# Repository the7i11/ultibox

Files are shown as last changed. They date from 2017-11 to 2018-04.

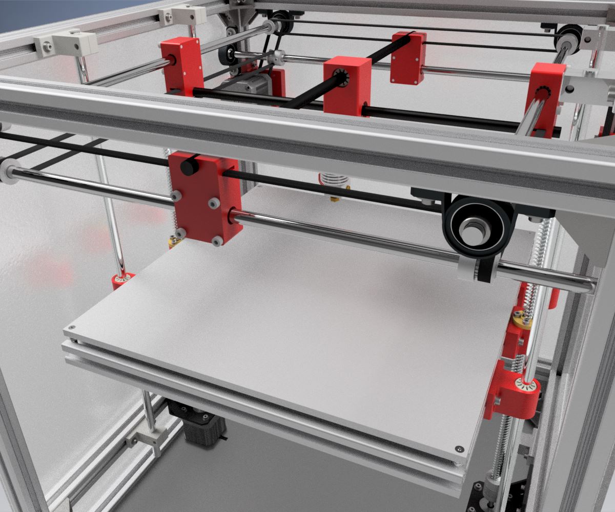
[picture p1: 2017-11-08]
media/prebuild render 05.jpg

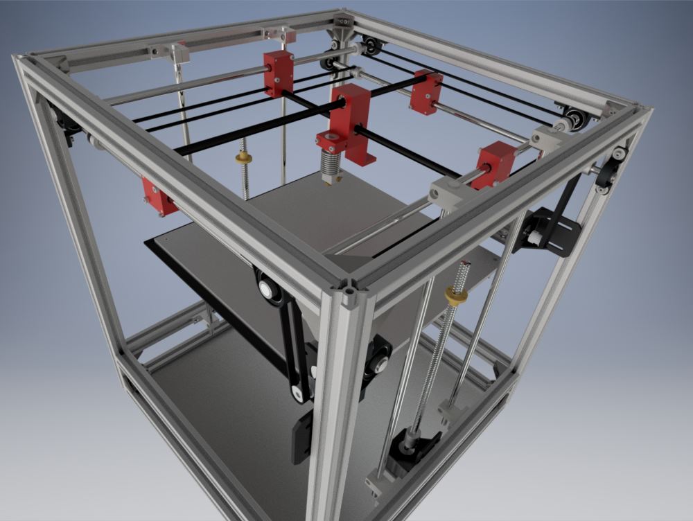
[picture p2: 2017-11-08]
media/prebuild render 03.jpg

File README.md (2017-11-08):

# Ultibox

Files for the Ultibox 3D-Printer. Please keep in mind that this project is in an early state. 
Several Ultibox 3D printers are ready-to-print at this moment, yet the project needs much work to be done.

The CAD files are created using Autodesk Inventor, but you can also use Autodesk Fusion360 to open them.

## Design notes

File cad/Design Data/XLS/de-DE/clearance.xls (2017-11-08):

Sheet: ANSI UST
I | Reihenfolge -1
Schraubentyp | Größe | Wellendurchmesser |  |  | Schraubenkopfbemaßungen
 |  | Schließen | Normal | Grob | Durchmesser | Tiefe/Winkel | Schraubenkopftyp
Flachkopfmaschinenschraube (82) | #0 | 0.0635 | 0.07 | 0.073 | 0.119 | 82 | 2
Flachkopfmaschinenschraube (82) | #1 | 0.076 | 0.081 | 0.089 | 0.146 | 82 | 2
Flachkopfmaschinenschraube (82) | #2 | 0.089 | 0.096 | 0.1065 | 0.172 | 82 | 2
Flachkopfmaschinenschraube (82) | #3 | 0.104 | 0.11 | 0.12 | 0.199 | 82 | 2
Flachkopfmaschinenschraube (82) | #4 | 0.116 | 0.1285 | 0.136 | 0.225 | 82 | 2
Flachkopfmaschinenschraube (82) | #5 | 0.1285 | 0.136 | 0.154 | 0.252 | 82 | 2
Flachkopfmaschinenschraube (82) | #6 | 0.144 | 0.1495 | 0.1695 | 0.279 | 82 | 2
Flachkopfmaschinenschraube (82) | #8 | 0.1695 | 0.177 | 0.1935 | 0.332 | 82 | 2
Flachkopfmaschinenschraube (82) | #10 | 0.196 | 0.201 | 0.221 | 0.385 | 82 | 2
Flachkopfmaschinenschraube (82) | #12 | 0.221 | 0.228 | 0.246 | 0.438 | 82 | 2
Flachkopfmaschinenschraube (82) | 1/4 | 0.257 | 0.266 | 0.2812 | 0.507 | 82 | 2
Flachkopfmaschinenschraube (82) | 5/16 | 0.323 | 0.332 | 0.3437 | 0.635 | 82 | 2
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

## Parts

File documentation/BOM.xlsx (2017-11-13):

 | Item | Count | Single | Overall
Frame
 | Aluminium extrusion 500mm | 4 | 1.34 € | 5.36 € |  | http://www.motedis.com/shop/Nutprofil/20-B-Typ-Nut-6/Aluprofil-20x20-B-Typ-Nut-6::1.html
 | Aluminium extrusion 400mm | 16 | 1.08 € | 17.28 €
 | 10 corner pieces | 4 | 2.71 € | 10.84 € |  | http://www.banggood.com/10pcs-20x20mm-Aluminium-Corner-Joint-Right-Angle-Bracket-Furniture-Fittings-p-1056722.html
 | 50 T-Nuts M3 | 2 | 3.89 € | 7.78 € |  | http://www.banggood.com/50pcs-M3-T-Sliding-Nut-Zin-Plated-Carbon-Steel-T-Sliding-Nut-for-2020-Aluminum-Profile-p-1081131.html
 | 50 M3 Washers | 2 | 1.08 € | 2.16 € |  | http://www.banggood.com/50-PCS-Stainless-Steel-Flat-Gasket-Plain-Washer-Spacer-M390_8-For-M3-Motor-Shalf-p-1064061.html
 | 100 M3x8 mm | 2 | 1.85 € | 3.70 € |  | https://www.amazon.de/St%C3%BCck-Zylinderkopfschrauben-Edelstahl-Zylinderschrauben-Innensechskant/dp/B018XL758M
 | 100 M3x20mm | 1 | 2.09 € | 2.09 € |  | https://www.amazon.de/St%C3%BCck-Zylinderkopfschrauben-Edelstahl-Zylinderschrauben-Innensechskant/dp/B018XL6B6O
 |  |  |  |  | 49.21 €
UM-Gantry
 | 2x 400 x 6mm rail | 1 | 6.89 € | 6.89 € |  | https://de.aliexpress.com/item/2-Pcs-Cnc-Linear-Shaft-Chrome-OD-6mm-L-400mm-WCS-Round-Hardened-Steel-Rod-Bar/32791713155.html
 | 4x LM8UU-formfactor bronze bushings | 1 | 7.04 € | 7.04 € |  | https://de.aliexpress.com/item/4pcs-8x15x24-mm-linear-graphite-copper-set-bearing-copper-bushing-oil-self-lubricating-bearing-JDB-Free/32823893175.html
 | 5m GT2 Belt + 4 20T Pulleys | 1 | 7.27 € | 7.27 € |  | http://www.banggood.com/GT2-Aluminium-Timing-Pulley-20-Teeth-M4-Screw-5M-Belt-For-RepRap-3D-Printer-Prusa-CNC-p-1081285.html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
 | GT2 20T double pulley 8mm bore | 2 | 1.49 € | 2.98 € |  | https://de.aliexpress.com/item/1Pcs-ultimaker-2-DIY-2GT-GT2-Timing-Driving-Pulley-20-Tooth-20teeth-Bore-5mm-8mm-Double/32640966282.html
 | 10x GT2 20T pulley 8mm bore | 1 | 8.84 € | 8.84 € |  | https://de.aliexpress.com/item/Wholesale-10pcs-20-teeth-Bore-8mm-GT2-Timing-Pulley-fit-width-6mm-of-2GT-Belt-3D/32616479146.html
 | 500 x 8mm rail | 8 | 5.95 € | 47.60 € |  | http://www.ebay.de/itm/ETGCR15-8-mm-Linearwelle-gehartet-aus-GCR15-verchromt-8-mm-Durchmesser-500-mm-/162078170839
 | 10x KP08 flanged bearing | 1 | 11.50 € | 11.50 € |  | https://de.aliexpress.com/item/NEW-10pcs-lot-8-mm-caliber-Zinc-Alloy-mounted-bearings-KP08-UCP08-P08-pillow-block-bearing/32368432549.html
 | 2x LM6LUU linear bearing | 2 | 1.00 € | 2.00 € |  | https://de.aliexpress.com/item/Free-shipping-2-pcs-lot-LM6LUU-LML6UU-6x12x35mm-6mm-Long-linear-ball-bearing-bush-bushing-Ultimaker/32727750790.html
 |  |  |  |  | 92.12 €
Z-Achse
 | Trapezoidal spindle 300mm | 2 | 2.98 € | 5.96 € |  | https://de.aliexpress.com/item/3D-Printer-THSL-300-8D-Lead-Screw-Dia-8MM-Thread-8mm-Length-300mm-trapezoidal-spindle-screw/32804077178.html
 | 4x SK8 linear rail support | 1 | 3.59 € | 3.59 € |  | https://de.aliexpress.com/item/4PCS-LOT-linear-rail-shaft-8mm-SK8-SH8A-Linear-Rail-Shaft-Support-XYZ-Table-CNC-and/32815287740.html
 | 5x8mm coupling | 2 | 1.18 € | 2.36 € |  | https://de.aliexpress.com/item/5x8-mm-Motor-Jaw-Shaft-Coupler-5mm-To-8mm-Flexible-Coupling-OD-19x25mm-Whoelsale/32615723244.html
 |  |  |  |  | 11.91 €
Extruder
 | E3D V6 all-metall clone | 1 | 8.63 € | 8.63 € |  | http://www.banggood.com/0_4mm-E3D-V6-All-metal-3D-Printer-Extrusion-Head-Nozzle-With-Fan-p-1036420.html
 | E3D Titan extruder clone | 1 | 12.87 € | 12.87 € |  | https://de.aliexpress.com/item/BIGTREETECH-Titan-Extruder-Fully-Kits-for-Titan-Extruder-for-1-75mm-Nema-17-Stepper-Motor-V6/32789942768.html
 | Induktiver proximity sensor | 1 | 1.88 € | 1.88 € |  | https://de.aliexpress.com/item/1pcs-M8-2mm-Sensing-Inductive-Proximity-Sensor-Switch-NPN-Work-Voltage-5V-DC-Special-For-MCU/32825728358.html
 | 40mm 24V fan | 1 | 0.87 € | 0.87 € |  | https://de.aliexpress.com/item/24V-2-Pin-DC-Cooling-Fan-40mm-40x40x10mm-4cm-4010s-9Blade-For-3D-Printer-CPU/32804862157.html
 |  |  |  |  | 24.25 €
Elektronik
 | Smoothieboard | 1 | 38.61 € | 38.61 € |  | https://de.aliexpress.com/item/3Dpriter-control-board-MKS-SBase-V1-0-32-s-Motherboard-compatible-Smoothieware-open-source-firmware-support/32384368763.html
 | Silikon heater matt 300x300mm | 1 | 13.94 € | 13.94 € |  | https://www.aliexpress.com/item/1pcs-silicone-heating-pad-heater-220V-600W-300-300-mm-for-3d-printer-heat-bed/32591046539.html
 | NEMA 17 stepper 0,9° 46N/cm | 2 | 12.90 € | 25.80 € |  | https://www.omc-stepperonline.com/hybrid-stepper-motor/nema-17-bipolar-09deg-46ncm-651ozin-2a-28v-42x42x48mm-4-wires-17hm19-2004s.html
 | NEMA 17 stepper 1,8° 36N/cm | 3 | 9.41 € | 28.23 € |  | https://www.omc-stepperonline.com/hybrid-stepper-motor/nema-17-bipolar-18deg-36ncm-51ozin-085a-54v-42x42x39mm-4-wires-17hs15-0854s.html
 | NEMA 17 stepper 1,8° 65N/cm | 0 | 10.26 € | 0.00 € |  | https://www.omc-stepperonline.com/hybrid-stepper-motor/nema-17-bipolar-18deg-65ncm-92ozin-21a-336v-42x42x60mm-4-wires-17hs24-2104s.html
 | 24V 5A powersupply | 1 | 12.54 € | 12.54 € |  | https://de.aliexpress.com/item/Universal-24V-5A-120W-Regulated-Switching-Power-Supply-Transformer-100-240V-AC-to-DC-For-LED/32606322171.html
 | 25A SSR 480V AC | 1 | 4.53 € | 4.53 € |  | http://www.banggood.com/SSR-25DA-SSR-Solid-state-Solid-State-Relay-25A-Output-AC24-380V-p-79300.html
 | 10 Microswitches | 1 | 1.70 € | 1.70 € |  | https://de.aliexpress.com/item/Low-Price-10pcs-Lot-3-Pin-Tact-Switch-Sensitive-Microswitch-With-Round-Handle-KW11-3Z-5A/32700243989.html
 |  |  |  |  | 125.35 €
Sonstiges
 | Fine milled aluminium plate 315x315x6mm | 1 | 34.76 € | 34.76 € |  | https://www.aluminium-online-shop.de
 | NEMA 17 mount | 2 | 2.91 € | 5.82 € |  | https://de.aliexpress.com/item/3d-printer-Accessories-NEMA17-Mounting-L-Bracket-Mount-42-series-Stepper-Motor-Alloy-Steel-Mounting-Bracket/32659632755.html
 | 50x M3 square nuts | 1 | 0.87 € | 0.87 € |  | https://de.aliexpress.com/item/100pcs-M3-color-zinc-plated-square-nuts-block-square-quadrangle-quadrilateral-galvanized-square-nuts-hw55028/32666611009.html
 |  |  |  |  | 41.45 €
 |  |  |  |  | 344.29
 |  |  |  |  |  | https://de.aliexpress.com/item/280-280-1-5mm-Silicone-Rubber-3D-Printer-Heater-220V-450w-3M-adhesive-2-face-130C/32666160575.html

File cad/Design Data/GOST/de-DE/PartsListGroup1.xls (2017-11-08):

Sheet: Лист 1
Инв. № подл |  |  |  | Подп. и дата | Взам. инв. № | Инв. № дубл. |  |  | Подп. и дата
Формат | Зона | Поз. | Обозначение |  |  |  | Наименование |  |  |  |  |  | Кол. на исполнение
 |  |  |  |  |  |  |  |  |  |  |  | Лит.
 |  |  |  |  |  |  |  |  |  |  |  | Код
 |  |  |  |  |  |  |  | Изм. | Лист | № докум | Подпись |  | Дата
 |  |  |  |  |  |  |  | Разраб.
 |  |  |  |  |  |  |  | Пров.
 |  |  |  |  |  |  |  | Н.контр
 |  |  |  |  |  |  |  | Утв.
 |  |  |  |  |  |  |  |  |  |  |  |  |  | Копировал

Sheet: Лист 2
Инв. № подл |  |  |  | Подп. и дата | Взам. инв. № | Инв. № дубл. |  |  | Подп. и дата
Формат | Зона | Поз. | Обозначение |  |  |  | Наименование |  |  |  |  | Кол. на исполнение
 |  |  |  |  |  |  |  | Изм. | Лист | № докум. | Подп. | Дата
 |  |  |  |  |  |  |  |  |  |  |  |  | Копировал
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

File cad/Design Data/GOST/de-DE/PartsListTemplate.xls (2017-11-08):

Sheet: Лист 1
 | Формат | Зона |  | Поз. |  | Обозначение |  |  |  | Наименование |  |  |  | Кол. | Приме-чание
Подп. и дата
Инв. № дубл.
Взам. инв. №
Подп. и дата
 | Изм. |  | Лист |  | № докум |  | Подпись | Дата
Инв. № подл | Разраб. |  |  |  |  |  |  |  |  |  | Литера |  | Лист |  |  | Листов
 | Пров.
 | Н.контр
 | Утв.
 |  |  |  |  |  |  |  |  | Копировал |  |  | Формат А4

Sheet: Лист 2
 | Формат | Зона |  | Поз. |  | Обозначение |  |  |  | Наименование |  | Кол. | Приме-чание
Подп. и дата
Инв. № дубл.
Взам. инв. №
Подп. и дата
Инв. № подл
 | Изм. |  | Лист |  | № докум. |  | Подп. |  | Дата
 |  |  |  |  |  |  |  | Копировал |  |  | Формат А4
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

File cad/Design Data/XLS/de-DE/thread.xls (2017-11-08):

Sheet: Inch Tapping Threads
I Q X | Zoll-Blechschraubgewinde |  | Sort Order - 5 |  | External |  |  |  |  |  |  | Internal
 |  |  |  |  |  | Major Dia |  | Pitch Dia |  | Minor Dia |  |  | Minor Dia |  | Pitch Dia |  | Major Dia |  | Tap Drill
Size | Size Suffix | Thread Designation | Custom Thread Designation | TPI | Class | Max | Min | Max | Min | Max | Min | Class | Min | Max | Min | Max | Min | Max | Basic
0.0600 |  | 0-48 | 0-48 | 48 | 2B | 0.0600 | 0.0540 | 0.0480 | 0.0435 | 0.0360 | 0.0330
0.0730 |  | 1-42 | 1-42 | 42 | 2B | 0.0750 | 0.0690 | 0.0620 | 0.0575 | 0.0490 | 0.0460
0.0860 |  | 2-32 | 2-32 | 32 | 2B | 0.0880 | 0.0820 | 0.0760 | 0.0710 | 0.0640 | 0.0600
0.0990 |  | 3-28 | 3-28 | 28 | 2B | 0.1010 | 0.0950 | 0.0880 | 0.0830 | 0.0750 | 0.0710
0.1120 |  | 4-24 | 4-24 | 24 | 2B | 0.1140 | 0.1080 | 0.1000 | 0.0950 | 0.0860 | 0.0820
0.1250 |  | 5-20 | 5-20 | 20 | 2B | 0.1300 | 0.1230 | 0.1120 | 0.1065 | 0.0940 | 0.0900
0.1380 |  | 6-20 | 6-20 | 20 | 2B | 0.1390 | 0.1320 | 0.1215 | 0.1155 | 0.1040 | 0.0990
0.1510 |  | 7-19 | 7-19 | 19 | 2B | 0.1540 | 0.1470 | 0.1345 | 0.1280 | 0.1150 | 0.1090
0.1640 |  | 8-18 | 8-18 | 18 | 2B | 0.1660 | 0.1590 | 0.1440 | 0.1375 | 0.1220 | 0.1160
0.1900 |  | 10-16 | 10-16 | 16 | 2B | 0.1890 | 0.1820 | 0.1650 | 0.1585 | 0.1410 | 0.1350
0.2160 |  | 12-14 | 12-14 | 14 | 2B | 0.2150 | 0.2080 | 0.1895 | 0.1825 | 0.1640 | 0.1570
0.2420 |  | 14-14 | 14-14 | 14 | 2B | 0.2410 | 0.2340 | 0.2130 | 0.2060 | 0.1850 | 0.1780
0.2500 |  | 1/4-14 | 1/4-14 | 14 | 2B | 0.2460 | 0.2370 | 0.2190 | 0.2110 | 0.1920 | 0.1850
0.3125 |  | 5/16-12 | 5/16-12 | 12 | 2B | 0.3150 | 0.3060 | 0.2795 | 0.2710 | 0.2440 | 0.2360
0.3750 |  | 3/8-12 | 3/8-12 | 12 | 2B | 0.3800 | 0.3710 | 0.3445 | 0.3350 | 0.3090 | 0.2990
0.4375 |  | 7/16-10 | 7/16-10 | 10 | 2B | 0.4400 | 0.4290 | 0.3995 | 0.3890 | 0.3590 | 0.3490
0.5000 |  | 1/2-10 | 1/2-10 | 10 | 2B | 0.5040 | 0.4930 | 0.4635 | 0.4530 | 0.4230 | 0.4130

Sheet: Metric Forming Screw Threads
M P X | Metrisch geform. Schraubgewinde |  | Sort Order - 6 |  | External |  |  |  |  |  |  | Internal
 |  |  |  |  |  | Major Dia |  | Pitch Dia |  | Minor Dia |  |  | Minor Dia |  | Pitch Dia |  | Major Dia |  | Tap Drill
Size | Size Suffix | Thread Designation | Custom Thread Designation | Pitch | Class | Max | Min | Max | Min | Max | Min | Class | Min | Max | Min | Max | Min | Max | Basic
1.5 |  | 1.5x0.5 | 1.5x0.5 | 0.5 | 6g | 1.520 | 1.380 | 1.215 | 1.110 | 0.910 | 0.840
1.5 |  | ST1.5x0.5 | ST1.5x0.5 | 0.5 | 6g | 1.520 | 1.380 | 1.215 | 1.110 | 0.910 | 0.840
1.9 |  | 1.9x0.6 | 1.9x0.6 | 0.6 | 6g | 1.900 | 1.760 | 1.570 | 1.465 | 1.240 | 1.170
1.9 |  | ST1.9x0.6 | ST1.9x0.6 | 0.6 | 6g | 1.900 | 1.760 | 1.570 | 1.465 | 1.240 | 1.170
2.2 |  | 2.2x0.8 | 2.2x0.8 | 0.8 | 6g | 2.240 | 2.100 | 1.935 | 1.810 | 1.630 | 1.520
2.2 |  | ST2.2x0.8 | ST2.2x0.8 | 0.8 | 6g | 2.240 | 2.100 | 1.935 | 1.810 | 1.630 | 1.520
2.6 |  | 2.6x0.9 | 2.6x0.9 | 0.9 | 6g | 2.570 | 2.430 | 2.235 | 2.115 | 1.900 | 1.800
2.6 |  | ST2.6x0.9 | ST2.6x0.9 | 0.9 | 6g | 2.570 | 2.430 | 2.235 | 2.115 | 1.900 | 1.800
2.9 |  | 2.9x1 | 2.9x1 | 1 | 6g | 2.900 | 2.760 | 2.540 | 2.420 | 2.180 | 2.080
2.9 |  | 2.9x1.1 | 2.9x1.1 | 1.1 | 6g | 2.900 | 2.760 | 2.540 | 2.420 | 2.180 | 2.080
2.9 |  | ST2.9x1.1 | ST2.9x1.1 | 1.1 | 6g | 2.900 | 2.760 | 2.540 | 2.420 | 2.180 | 2.080
2.9 |  | 2.9x1.3 | 2.9x1.3 | 1.3 | 6g | 2.900 | 2.720 | 2.540 | 2.355 | 1.890 | 1.700
2.9 |  | 2.9x1.4 | 2.9x1.4 | 1.4 | 6g | 2.900 | 2.720 | 2.340 | 2.175 | 1.780 | 1.630
3.3 |  | 3.3x1.3 | 3.3x1.3 | 1.3 | 6g | 3.300 | 3.120 | 2.795 | 2.665 | 2.290 | 2.210
3.3 |  | ST3.3x1.3 | ST3.3x1.3 | 1.3 | 6g | 3.300 | 3.120 | 2.795 | 2.665 | 2.290 | 2.210
3.5 |  | 3.5x1.3 | 3.5x1.3 | 1.3 | 6g | 3.530 | 3.350 | 3.085 | 2.930 | 2.640 | 2.510
3.5 |  | ST3.5x1.3 | ST3.5x1.3 | 1.3 | 6g | 3.530 | 3.350 | 3.085 | 2.930 | 2.640 | 2.510
3.5 |  | 3.5x1.6 | 3.5x1.6 | 1.6 | 6g | 3.530 | 3.350 | 2.920 | 2.755 | 2.310 | 2.160
3.5 |  | 3.5x3.2 | 3.5x3.2 | 3.2 | 6g | 3.530 | 3.310 | 2.800 | 2.600 | 2.070 | 1.890
3.9 |  | 3.9x1.3 | 3.9x1.3 | 1.3 | 6g | 3.910 | 3.730 | 3.415 | 3.250 | 2.920 | 2.770
3.9 |  | ST3.9x1.3 | ST3.9x1.3 | 1.3 | 6g | 3.910 | 3.730 | 3.415 | 3.250 | 2.920 | 2.770
3.9 |  | 3.9x1.6 | 3.9x1.6 | 1.6 | 6g | 3.910 | 3.730 | 3.300 | 3.135 | 2.690 | 2.540
3.9 |  | 3.9x3.2 | 3.9x3.2 | 3.2 | 6g | 3.910 | 3.690 | 3.180 | 2.980 | 2.450 | 2.270
4.2 |  | 4.2x1.4 | 4.2x1.4 | 1.4 | 6g | 4.220 | 4.040 | 3.660 | 3.495 | 3.100 | 2.950
4.2 |  | ST4.2x1.4 | ST4.2x1.4 | 1.4 | 6g | 4.220 | 4.040 | 3.660 | 3.495 | 3.100 | 2.950
4.2 |  | 4.2x1.6 | 4.2x1.6 | 1.6 | 6g | 4.220 | 4.040 | 3.610 | 3.445 | 3.000 | 2.850
4.2 |  | 4.2x3.2 | 4.2x3.2 | 3.2 | 6g | 4.220 | 4.000 | 3.380 | 3.180 | 2.540 | 2.360
4.8 |  | 4.8x1.6 | 4.8x1.6 | 1.6 | 6g | 4.800 | 4.620 | 4.190 | 4.025 | 3.580 | 3.430
4.8 |  | ST4.8x1.6 | ST4.8x1.6 | 1.6 | 6g | 4.800 | 4.620 | 4.190 | 4.025 | 3.580 | 3.430
4.8 |  | 4.8x1.8 | 4.8x1.8 | 1.8 | 6g | 4.800 | 4.620 | 4.065 | 3.885 | 3.330 | 3.150
4.8 |  | 4.8x3.2 | 4.8x3.2 | 3.2 | 6g | 4.800 | 4.580 | 3.960 | 3.760 | 3.120 | 2.940
5.5 |  | 5.5x1.8 | 5.5x1.8 | 1.8 | 6g | 5.460 | 5.280 | 4.815 | 4.635 | 4.170 | 3.990
5.5 |  | ST5.5x1.8 | ST5.5x1.8 | 1.8 | 6g | 5.460 | 5.280 | 4.815 | 4.635 | 4.170 | 3.990
6.3 |  | 6.3x1.8 | 6.3x1.8 | 1.8 | 6g | 6.250 | 6.030 | 5.565 | 5.365 | 4.880 | 4.700
6.3 |  | ST6.3x1.8 | ST6.3x1.8 | 1.8 | 6g | 6.250 | 6.030 | 5.565 | 5.365 | 4.880 | 4.700
8.0 |  | 8x2.1 | 8x2.1 | 2.1 | 6g | 8.000 | 7.780 | 7.100 | 6.885 | 6.200 | 5.990
8.0 |  | ST8x2.1 | ST8x2.1 | 2.1 | 6g | 8.000 | 7.780 | 7.100 | 6.885 | 6.200 | 5.990
9.5 |  | 9.5x2.1 | 9.5x2.1 | 2.1 | 6g | 9.650 | 9.430 | 8.750 | 8.510 | 7.850 | 7.590
9.5 |  | ST9.5x2.1 | ST9.5x2.1 | 2.1 | 6g | 9.650 | 9.430 | 8.750 | 8.510 | 7.850 | 7.590

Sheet: ISO Pipe Threads
M Q | ISO-Rohrgewinde |  | Sort Order - 9 |  | External |  |  |  |  |  |  | Internal
 |  |  |  |  |  | Major Dia |  | Pitch Dia |  | Minor Dia |  |  | Minor Dia |  | Pitch Dia |  | Major Dia |  | Tap Drill | Thread Depth | Thread Runouts
Size | Size Suffix | Thread Designation | Custom Thread Designation | TPI | Class | Max | Min | Max | Min | Max | Min | Class | Min | Max | Min | Max | Min | Max | Basic
7.723 |  | G7.723x0.907 | G 1/16 | 28 | A | 7.723 | 7.509 | 7.142 | 7.035 | 6.561 |  |  | 6.561 | 6.834 | 7.142 | 7.249 | 7.723 |  | 1.5875 | 15.446 | 4.5000
7.723 |  | G7.723x0.907 | G 1/16 | 28 | B | 7.723 | 7.509 | 7.142 | 6.928 | 6.561
9.728 |  | G9.728x0.907 | G 1/8 | 28 | A | 9.728 | 9.514 | 9.147 | 9.040 | 8.566 |  |  | 8.566 | 8.848 | 9.147 | 9.254 | 9.728 |  | 3.1750 | 19.456 | 4.5000
9.728 |  | G9.728x0.907 | G 1/8 | 28 | B | 9.728 | 9.514 | 9.147 | 8.933 | 8.566
13.157 |  | G13.157x1.337 | G 1/4 | 19 | A | 13.157 | 12.907 | 12.301 | 12.176 | 11.445 |  |  | 11.445 | 11.89 | 12.301 | 12.426 | 13.157 |  | 6.3500 | 26.314 | 6.5000
13.157 |  | G13.157x1.337 | G 1/4 | 19 | B | 13.157 | 12.907 | 12.301 | 12.051 | 11.445
16.662 |  | G16.662x1.337 | G 3/8 | 19 | A | 16.662 | 16.412 | 15.806 | 15.681 | 14.950 |  |  | 14.95 | 15.395 | 15.806 | 15.931 | 16.662 |  | 9.5250 | 33.324 | 6.5000
16.662 |  | G16.662x1.337 | G 3/8 | 19 | B | 16.662 | 16.412 | 15.806 | 15.556 | 14.950
20.955 |  | G20.955x1.814 | G 1/2 | 14 | A | 20.955 | 20.671 | 19.793 | 19.651 | 18.631 |  |  | 18.631 | 19.172 | 19.793 | 19.935 | 20.955 |  | 12.7000 | 41.910 | 8.5000
20.955 |  | G20.955x1.814 | G 1/2 | 14 | B | 20.955 | 20.671 | 19.793 | 19.509 | 18.631
22.911 |  | G22.911x1.814 | G 5/8 | 14 | A | 22.911 | 22.627 | 21.749 | 21.607 | 20.587 |  |  | 20.587 | 21.128 | 21.749 | 21.891 | 22.911 |  |  | 45.822 | 8.5000
22.911 |  | G22.911x1.814 | G 5/8 | 14 | B | 22.911 | 22.627 | 21.749 | 21.465 | 20.587
26.441 |  | G26.441x1.814 | G 3/4 | 14 | A | 26.441 | 26.157 | 25.279 | 25.137 | 24.117 |  |  | 24.117 | 24.658 | 25.279 | 25.421 | 26.441 |  | 15.8750 | 52.882 | 8.5000
26.441 |  | G26.441x1.814 | G 3/4 | 14 | B | 26.441 | 26.157 | 25.279 | 24.995 | 24.117
30.201 |  | G30.201x1.814 | G 7/8 | 14 | A | 30.201 | 29.917 | 29.039 | 28.897 | 27.877 |  |  | 27.877 | 28.418 | 29.039 | 29.181 | 30.201 |  | 22.2250 | 60.402 | 8.5000
30.201 |  | G30.201x1.814 | G 7/8 | 14 | B | 30.201 | 29.917 | 29.039 | 28.755 | 27.877
33.249 |  | G33.249x2.309 | G 1 | 11 | A | 33.249 | 32.889 | 31.770 | 31.590 | 30.291 |  |  | 30.291 | 30.931 | 31.77 | 31.95 | 33.249 |  | 25.4000 | 66.498 | 10.0000
33.249 |  | G33.249x2.309 | G 1 | 11 | B | 33.249 | 32.889 | 31.770 | 31.410 | 30.291
37.897 |  | G37.897x2.309 | G 1 1/8 | 11 | A | 37.897 | 37.537 | 36.418 | 36.238 | 34.939 |  |  | 34.939 | 35.579 | 36.418 | 36.598 | 37.897 |  | 28.5750 | 75.794 | 10.0000
37.897 |  | G37.897x2.309 | G 1 1/8 | 11 | B | 37.897 | 37.537 | 36.418 | 36.058 | 34.939
41.910 |  | G41.91x2.309 | G 1 1/4 | 11 | A | 41.910 | 41.550 | 40.431 | 40.251 | 38.952 |  |  | 38.952 | 39.592 | 40.431 | 40.611 | 41.910 |  | 31.7500 | 83.820 | 10.0000
41.910 |  | G41.91x2.309 | G 1 1/4 | 11 | B | 41.910 | 41.550 | 40.431 | 40.071 | 38.952
47.803 |  | G47.803x2.309 | G 1 1/2 | 11 | A | 47.803 | 47.443 | 46.324 | 46.144 | 44.845 |  |  | 44.845 | 45.485 | 46.324 | 46.504 | 47.803 |  | 38.1000 | 95.606 | 10.0000
47.803 |  | G47.803x2.309 | G 1 1/2 | 11 | B | 47.803 | 47.443 | 46.324 | 45.964 | 44.845
53.746 |  | G53.746x2.309 | G 1 3/4 | 11 | A | 53.746 | 53.386 | 52.267 | 52.087 | 50.788 |  |  | 50.788 | 51.428 | 52.267 | 52.447 | 53.746 |  | 44.4500 | 107.492 | 10.0000
53.746 |  | G53.746x2.309 | G 1 3/4 | 11 | B | 53.746 | 53.386 | 52.267 | 51.907 | 50.788
59.614 |  | G59.614x2.309 | G 2 | 11 | A | 59.614 | 59.254 | 58.135 | 57.955 | 56.656 |  |  | 56.656 | 57.296 | 58.135 | 58.315 | 59.614 |  | 50.8000 | 119.228 | 10.0000
59.614 |  | G59.614x2.309 | G 2 | 11 | B | 59.614 | 59.254 | 58.135 | 57.775 | 56.656
65.710 |  | G65.71x2.309 | G 2 1/4 | 11 | A | 65.710 | 65.276 | 64.231 | 64.014 | 62.752 |  |  | 62.752 | 63.392 | 64.231 | 64.448 | 65.710 |  | 57.1500 | 131.420 | 10.0000
65.710 |  | G65.71x2.309 | G 2 1/4 | 11 | B | 65.710 | 65.276 | 64.231 | 63.797 | 62.752
75.184 |  | G75.184x2.309 | G 2 1/2 | 11 | A | 75.184 | 74.750 | 73.705 | 73.488 | 72.226 |  |  | 72.226 | 72.866 | 73.705 | 73.922 | 75.184 |  |  | 150.368 | 10.0000
75.184 |  | G75.184x2.309 | G 2 1/2 | 11 | B | 75.184 | 74.750 | 73.705 | 73.271 | 72.226
81.534 |  | G81.534x2.309 | G 2 3/4 | 11 | A | 81.534 | 81.100 | 80.055 | 79.838 | 78.576 |  |  | 78.576 | 79.216 | 80.055 | 80.272 | 81.534 |  | 69.8500 | 163.068 | 10.0000
81.534 |  | G81.534x2.309 | G 2 3/4 | 11 | B | 81.534 | 81.100 | 80.055 | 79.621 | 78.576
87.884 |  | G87.884x2.309 | G 3 | 11 | A | 87.884 | 87.450 | 86.405 | 86.188 | 84.926 |  |  | 84.926 | 85.566 | 86.405 | 86.622 | 87.884 |  | 76.2000 | 175.768 | 10.0000
87.884 |  | G87.884x2.309 | G 3 | 11 | B | 87.884 | 87.450 | 86.405 | 85.971 | 84.926
100.330 |  | G100.33x2.309 | G 3 1/2 | 11 | A | 100.330 | 99.896 | 98.851 | 98.634 | 97.372 |  |  | 97.372 | 98.012 | 98.851 | 99.068 | 100.330 |  | 88.9000 | 200.660 | 10.0000
100.330 |  | G100.33x2.309 | G 3 1/2 | 11 | B | 100.330 | 99.896 | 98.851 | 98.417 | 97.372
113.030 |  | G113.03x2.309 | G 4 | 11 | A | 113.030 | 112.596 | 111.551 | 111.334 | 110.072 |  |  | 110.072 | 110.712 | 111.551 | 111.768 | 113.030 |  | 101.6000 | 226.060 | 10.0000
113.030 |  | G113.03x2.309 | G 4 | 11 | B | 113.030 | 112.596 | 111.551 | 111.117 | 110.072
125.730 |  | G125.73x2.309 | G 4 1/2 | 11 | A | 125.730 | 125.296 | 124.251 | 124.034 | 122.772 |  |  | 122.772 | 123.412 | 124.251 | 124.468 | 125.730 |  | 114.3000 | 251.460 | 10.0000
125.730 |  | G125.73x2.309 | G 4 1/2 | 11 | B | 125.730 | 125.296 | 124.251 | 123.817 | 122.772
138.430 |  | G138.43x2.309 | G 5 | 11 | A | 138.430 | 137.996 | 136.951 | 136.734 | 135.472 |  |  | 135.472 | 136.112 | 136.951 | 137.168 | 138.430 |  | 127.0000 | 276.860 | 10.0000
138.430 |  | G138.43x2.309 | G 5 | 11 | B | 138.430 | 137.996 | 136.951 | 136.517 | 135.472
151.130 |  | G151.13x2.309 | G 5 1/2 | 11 | A | 151.130 | 150.696 | 149.651 | 149.434 | 148.172 |  |  | 148.172 | 148.812 | 149.651 | 149.868 | 151.130 |  | 139.7000 | 302.260 | 10.0000
151.130 |  | G151.13x2.309 | G 5 1/2 | 11 | B | 151.130 | 150.696 | 149.651 | 149.217 | 148.172
163.830 |  | G163.83x2.309 | G 6 | 11 | A | 163.830 | 163.396 | 162.351 | 162.134 | 160.872 |  |  | 160.872 | 161.512 | 162.351 | 162.568 | 163.830 |  | 152.4000 | 327.660 | 10.0000
163.830 |  | G163.83x2.309 | G 6 | 11 | B | 163.830 | 163.396 | 162.351 | 161.917 | 160.872

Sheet: JIS Pipe Threads
M Q | JIS-Rohrgewinde |  | Sort Order -12 |  | External |  |  |  |  |  |  | Internal
 |  |  |  |  |  | Major Dia |  | Pitch Dia |  | Minor Dia |  |  | Minor Dia |  | Pitch Dia |  | Major Dia |  | Tap Drill | Thread Depth | Thread Runouts
Size | Size Suffix | Thread Designation | Custom Thread Designation | TPI | Class | Max | Min | Max | Min | Max | Min | Class | Min | Max | Min | Max | Min | Max | Basic |  | Basic
7.723 |  | G7.723x0.907 | G 1/16 | 28 | A | 7.723 | 7.509 | 7.142 | 7.035 | 6.561 |  |  | 6.561 | 6.834 | 7.142 | 7.249 | 7.723 |  | 1.5875 | 15.446 | 4.5000
7.723 |  | G7.723x0.907 | G 1/16 | 28 | B | 7.723 | 7.509 | 7.142 | 6.928 | 6.561
9.728 |  | G9.728x0.907 | G 1/8 | 28 | A | 9.728 | 9.514 | 9.147 | 9.040 | 8.566 |  |  | 8.566 | 8.848 | 9.147 | 9.254 | 9.728 |  | 3.1750 | 19.456 | 4.5000
9.728 |  | G9.728x0.907 | G 1/8 | 28 | B | 9.728 | 9.514 | 9.147 | 8.933 | 8.566
13.157 |  | G13.157x1.337 | G 1/4 | 19 | A | 13.157 | 12.907 | 12.301 | 12.176 | 11.445 |  |  | 11.445 | 11.89 | 12.301 | 12.426 | 13.157 |  | 6.3500 | 26.314 | 6.5000
13.157 |  | G13.157x1.337 | G 1/4 | 19 | B | 13.157 | 12.907 | 12.301 | 12.051 | 11.445
16.662 |  | G16.662x1.337 | G 3/8 | 19 | A | 16.662 | 16.412 | 15.806 | 15.681 | 14.950 |  |  | 14.95 | 15.395 | 15.806 | 15.931 | 16.662 |  | 9.5250 | 33.324 | 6.5000
16.662 |  | G16.662x1.337 | G 3/8 | 19 | B | 16.662 | 16.412 | 15.806 | 15.556 | 14.950
20.955 |  | G20.955x1.814 | G 1/2 | 14 | A | 20.955 | 20.671 | 19.793 | 19.651 | 18.631 |  |  | 18.631 | 19.172 | 19.793 | 19.935 | 20.955 |  | 12.7000 | 41.910 | 8.5000
20.955 |  | G20.955x1.814 | G 1/2 | 14 | B | 20.955 | 20.671 | 19.793 | 19.509 | 18.631
22.911 |  | G22.911x1.814 | G 5/8 | 14 | A | 22.911 | 22.627 | 21.749 | 21.607 | 20.587 |  |  | 20.587 | 21.128 | 21.749 | 21.891 | 22.911 |  |  | 45.822 | 8.5000
22.911 |  | G22.911x1.814 | G 5/8 | 14 | B | 22.911 | 22.627 | 21.749 | 21.465 | 20.587
26.441 |  | G26.441x1.814 | G 3/4 | 14 | A | 26.441 | 26.157 | 25.279 | 25.137 | 24.117 |  |  | 24.117 | 24.658 | 25.279 | 25.421 | 26.441 |  | 15.8750 | 52.882 | 8.5000
26.441 |  | G26.441x1.814 | G 3/4 | 14 | B | 26.441 | 26.157 | 25.279 | 24.995 | 24.117
30.201 |  | G30.201x1.814 | G 7/8 | 14 | A | 30.201 | 29.917 | 29.039 | 28.897 | 27.877 |  |  | 27.877 | 28.418 | 29.039 | 29.181 | 30.201 |  | 22.2250 | 60.402 | 8.8000
30.201 |  | G30.201x1.814 | G 7/8 | 14 | B | 30.201 | 29.917 | 29.039 | 28.755 | 27.877
33.249 |  | G33.249x2.309 | G 1 | 11 | A | 33.249 | 32.889 | 31.770 | 31.590 | 30.291 |  |  | 30.291 | 30.931 | 31.77 | 31.95 | 33.249 |  | 25.4000 | 66.498 | 10.0000
33.249 |  | G33.249x2.309 | G 1 | 11 | B | 33.249 | 32.889 | 31.770 | 31.410 | 30.291
37.897 |  | G37.897x2.309 | G 1 1/8 | 11 | A | 37.897 | 37.537 | 36.418 | 36.238 | 34.939 |  |  | 34.939 | 35.579 | 36.418 | 36.598 | 37.897 |  | 28.5750 | 75.794 | 10.0000
37.897 |  | G37.897x2.309 | G 1 1/8 | 11 | B | 37.897 | 37.537 | 36.418 | 36.058 | 34.939
41.910 |  | G41.91x2.309 | G 1 1/4 | 11 | A | 41.910 | 41.550 | 40.431 | 40.251 | 38.952 |  |  | 38.952 | 39.592 | 40.431 | 40.611 | 41.910 |  | 31.7500 | 83.820 | 10.0000
41.910 |  | G41.91x2.309 | G 1 1/4 | 11 | B | 41.910 | 41.550 | 40.431 | 40.071 | 38.952
47.803 |  | G47.803x2.309 | G 1 1/2 | 11 | A | 47.803 | 47.443 | 46.324 | 46.144 | 44.845 |  |  | 44.845 | 45.485 | 46.324 | 46.504 | 47.803 |  | 38.1000 | 95.606 | 10.0000
47.803 |  | G47.803x2.309 | G 1 1/2 | 11 | B | 47.803 | 47.443 | 46.324 | 45.964 | 44.845
53.746 |  | G53.746x2.309 | G 1 3/4 | 11 | A | 53.746 | 53.386 | 52.267 | 52.087 | 50.788 |  |  | 50.788 | 51.428 | 52.267 | 52.447 | 53.746 |  | 44.4500 | 107.492 | 10.0000
53.746 |  | G53.746x2.309 | G 1 3/4 | 11 | B | 53.746 | 53.386 | 52.267 | 51.907 | 50.788
59.614 |  | G59.614x2.309 | G 2 | 11 | A | 59.614 | 59.254 | 58.135 | 57.955 | 56.656 |  |  | 56.656 | 57.296 | 58.135 | 58.315 | 59.614 |  | 50.8000 | 119.228 | 10.0000
59.614 |  | G59.614x2.309 | G 2 | 11 | B | 59.614 | 59.254 | 58.135 | 57.775 | 56.656
65.710 |  | G65.71x2.309 | G 2 1/4 | 11 | A | 65.710 | 65.276 | 64.231 | 64.014 | 62.752 |  |  | 62.752 | 63.392 | 64.231 | 64.448 | 65.710 |  | 57.1500 | 131.420 | 10.0000
65.710 |  | G65.71x2.309 | G 2 1/4 | 11 | B | 65.710 | 65.276 | 64.231 | 63.797 | 62.752
75.184 |  | G75.184x2.309 | G 2 1/2 | 11 | A | 75.184 | 74.750 | 73.705 | 73.488 | 72.226 |  |  | 72.226 | 72.866 | 73.705 | 73.922 | 75.184 |  |  | 150.368 | 10.0000
75.184 |  | G75.184x2.309 | G 2 1/2 | 11 | B | 75.184 | 74.750 | 73.705 | 73.271 | 72.226
81.534 |  | G81.534x2.309 | G 2 3/4 | 11 | A | 81.534 | 81.100 | 80.055 | 79.838 | 78.576 |  |  | 78.576 | 79.216 | 80.055 | 80.272 | 81.534 |  | 69.8500 | 163.068 | 10.0000
81.534 |  | G81.534x2.309 | G 2 3/4 | 11 | B | 81.534 | 81.100 | 80.055 | 79.621 | 78.576
87.884 |  | G87.884x2.309 | G 3 | 11 | A | 87.884 | 87.450 | 86.405 | 86.188 | 84.926 |  |  | 84.926 | 85.566 | 86.405 | 86.622 | 87.884 |  | 76.2000 | 175.768 | 10.0000
87.884 |  | G87.884x2.309 | G 3 | 11 | B | 87.884 | 87.450 | 86.405 | 85.971 | 84.926
100.330 |  | G100.33x2.309 | G 3 1/2 | 11 | A | 100.330 | 99.896 | 98.851 | 98.634 | 97.372 |  |  | 97.372 | 98.012 | 98.851 | 99.068 | 100.330 |  | 88.9000 | 200.660 | 10.0000
100.330 |  | G100.33x2.309 | G 3 1/2 | 11 | B | 100.330 | 99.896 | 98.851 | 98.417 | 97.372
113.030 |  | G113.03x2.309 | G 4 | 11 | A | 113.030 | 112.596 | 111.551 | 111.334 | 110.072 |  |  | 110.072 | 110.712 | 111.551 | 111.768 | 113.030 |  | 101.6000 | 226.060 | 10.0000
113.030 |  | G113.03x2.309 | G 4 | 11 | B | 113.030 | 112.596 | 111.551 | 111.117 | 110.072
125.730 |  | G125.73x2.309 | G 4 1/2 | 11 | A | 125.730 | 125.296 | 124.251 | 124.034 | 122.772 |  |  | 122.772 | 123.412 | 124.251 | 124.468 | 125.730 |  | 114.3000 | 251.460 | 10.0000
125.730 |  | G125.73x2.309 | G 4 1/2 | 11 | B | 125.730 | 125.296 | 124.251 | 123.817 | 122.772
138.430 |  | G138.43x2.309 | G 5 | 11 | A | 138.430 | 137.996 | 136.951 | 136.734 | 135.472 |  |  | 135.472 | 136.112 | 136.951 | 137.168 | 138.430 |  | 127.0000 | 276.860 | 10.0000
138.430 |  | G138.43x2.309 | G 5 | 11 | B | 138.430 | 137.996 | 136.951 | 136.517 | 135.472
151.130 |  | G151.13x2.309 | G 5 1/2 | 11 | A | 151.130 | 150.696 | 149.651 | 149.434 | 148.172 |  |  | 148.172 | 148.812 | 149.651 | 149.868 | 151.130 |  | 139.7000 | 302.260 | 10.0000
151.130 |  | G151.13x2.309 | G 5 1/2 | 11 | B | 151.130 | 150.696 | 149.651 | 149.217 | 148.172
163.830 |  | G163.83x2.309 | G 6 | 11 | A | 163.830 | 163.396 | 162.351 | 162.134 | 160.872 |  |  | 160.872 | 161.512 | 162.351 | 162.568 | 163.830 |  | 152.4000 | 327.660 | 10.0000
163.830 |  | G163.83x2.309 | G 6 | 11 | B | 163.830 | 163.396 | 162.351 | 161.917 | 160.872

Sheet: DIN Pipe Threads
M Q | DIN-Rohrgewinde |  | Sort Order - 18 |  | External |  |  |  |  |  |  | Internal
 |  |  |  |  |  | Major Dia |  | Pitch Dia |  | Minor Dia |  |  | Minor Dia |  | Pitch Dia |  | Major Dia |  | Tap Drill | Thread Depth | Thread Runouts
Size | Size Suffix | Thread Designation | Custom Thread Designation | TPI | Class | Max | Min | Max | Min | Max | Min | Class | Min | Max | Min | Max | Min | Max | Basic
7.723 |  | G7.723x0.907 | G 1/16 | 28 | A | 7.723 | 7.509 | 7.142 | 7.035 | 6.561 |  |  | 6.561 | 6.834 | 7.142 | 7.249 | 7.723 |  | 1.5875 | 15.446 | 4.5000
7.723 |  | G7.723x0.907 | G 1/16 | 28 | B | 7.723 | 7.509 | 7.142 | 6.928 | 6.561
9.728 |  | G9.728x0.907 | G 1/8 | 28 | A | 9.728 | 9.514 | 9.147 | 9.040 | 8.566 |  |  | 8.566 | 8.848 | 9.147 | 9.254 | 9.728 |  | 3.1750 | 19.456 | 4.5000
9.728 |  | G9.728x0.907 | G 1/8 | 28 | B | 9.728 | 9.514 | 9.147 | 8.933 | 8.566
13.157 |  | G13.157x1.337 | G 1/4 | 19 | A | 13.157 | 12.907 | 12.301 | 12.176 | 11.445 |  |  | 11.445 | 11.89 | 12.301 | 12.426 | 13.157 |  | 6.3500 | 26.314 | 6.5000
13.157 |  | G13.157x1.337 | G 1/4 | 19 | B | 13.157 | 12.907 | 12.301 | 12.051 | 11.445
16.662 |  | G16.662x1.337 | G 3/8 | 19 | A | 16.662 | 16.412 | 15.806 | 15.681 | 14.950 |  |  | 14.95 | 15.395 | 15.806 | 15.931 | 16.662 |  | 9.5250 | 33.324 | 6.5000
16.662 |  | G16.662x1.337 | G 3/8 | 19 | B | 16.662 | 16.412 | 15.806 | 15.556 | 14.950
20.955 |  | G20.955x1.814 | G 1/2 | 14 | A | 20.955 | 20.671 | 19.793 | 19.651 | 18.631 |  |  | 18.631 | 19.172 | 19.793 | 19.935 | 20.955 |  | 12.7000 | 41.910 | 8.5000
20.955 |  | G20.955x1.814 | G 1/2 | 14 | B | 20.955 | 20.671 | 19.793 | 19.509 | 18.631
22.911 |  | G22.911x1.814 | G 5/8 | 14 | A | 22.911 | 22.627 | 21.749 | 21.607 | 20.587 |  |  | 20.587 | 21.128 | 21.749 | 21.891 | 22.911 |  |  | 45.822 | 8.5000
22.911 |  | G22.911x1.814 | G 5/8 | 14 | B | 22.911 | 22.627 | 21.749 | 21.465 | 20.587
26.441 |  | G26.441x1.814 | G 3/4 | 14 | A | 26.441 | 26.157 | 25.279 | 25.137 | 24.117 |  |  | 24.117 | 24.658 | 25.279 | 25.421 | 26.441 |  | 15.8750 | 52.882 | 8.5000
26.441 |  | G26.441x1.814 | G 3/4 | 14 | B | 26.441 | 26.157 | 25.279 | 24.995 | 24.117
30.201 |  | G30.201x1.814 | G 7/8 | 14 | A | 30.201 | 29.917 | 29.039 | 28.897 | 27.877 |  |  | 27.877 | 28.418 | 29.039 | 29.181 | 30.201 |  | 22.2250 | 60.402 | 8.5000
30.201 |  | G30.201x1.814 | G 7/8 | 14 | B | 30.201 | 29.917 | 29.039 | 28.755 | 27.877
33.249 |  | G33.249x2.309 | G 1 | 11 | A | 33.249 | 32.889 | 31.770 | 31.590 | 30.291 |  |  | 30.291 | 30.931 | 31.77 | 31.95 | 33.249 |  | 25.4000 | 66.498 | 10.5000
33.249 |  | G33.249x2.309 | G 1 | 11 | B | 33.249 | 32.889 | 31.770 | 31.410 | 30.291
37.897 |  | G37.897x2.309 | G 1 1/8 | 11 | A | 37.897 | 37.537 | 36.418 | 36.238 | 34.939 |  |  | 34.939 | 35.579 | 36.418 | 36.598 | 37.897 |  | 28.5750 | 75.794 | 10.5000
37.897 |  | G37.897x2.309 | G 1 1/8 | 11 | B | 37.897 | 37.537 | 36.418 | 36.058 | 34.939
41.910 |  | G41.91x2.309 | G 1 1/4 | 11 | A | 41.910 | 41.550 | 40.431 | 40.251 | 38.952 |  |  | 38.952 | 39.592 | 40.431 | 40.611 | 41.910 |  | 31.7500 | 83.820 | 10.5000
41.910 |  | G41.91x2.309 | G 1 1/4 | 11 | B | 41.910 | 41.550 | 40.431 | 40.071 | 38.952
47.803 |  | G47.803x2.309 | G 1 1/2 | 11 | A | 47.803 | 47.443 | 46.324 | 46.144 | 44.845 |  |  | 44.845 | 45.485 | 46.324 | 46.504 | 47.803 |  | 38.1000 | 95.606 | 10.5000
47.803 |  | G47.803x2.309 | G 1 1/2 | 11 | B | 47.803 | 47.443 | 46.324 | 45.964 | 44.845
53.746 |  | G53.746x2.309 | G 1 3/4 | 11 | A | 53.746 | 53.386 | 52.267 | 52.087 | 50.788 |  |  | 50.788 | 51.428 | 52.267 | 52.447 | 53.746 |  | 44.4500 | 107.492 | 10.5000
53.746 |  | G53.746x2.309 | G 1 3/4 | 11 | B | 53.746 | 53.386 | 52.267 | 51.907 | 50.788
59.614 |  | G59.614x2.309 | G 2 | 11 | A | 59.614 | 59.254 | 58.135 | 57.955 | 56.656 |  |  | 56.656 | 57.296 | 58.135 | 58.315 | 59.614 |  | 50.8000 | 119.228 | 10.5000
59.614 |  | G59.614x2.309 | G 2 | 11 | B | 59.614 | 59.254 | 58.135 | 57.775 | 56.656
65.710 |  | G65.71x2.309 | G 2 1/4 | 11 | A | 65.710 | 65.276 | 64.231 | 64.014 | 62.752 |  |  | 62.752 | 63.392 | 64.231 | 64.448 | 65.710 |  | 57.1500 | 131.420 | 10.5000
65.710 |  | G65.71x2.309 | G 2 1/4 | 11 | B | 65.710 | 65.276 | 64.231 | 63.797 | 62.752
75.184 |  | G75.184x2.309 | G 2 1/2 | 11 | A | 75.184 | 74.750 | 73.705 | 73.488 | 72.226 |  |  | 72.226 | 72.866 | 73.705 | 73.922 | 75.184 |  |  | 150.368 | 10.5000
75.184 |  | G75.184x2.309 | G 2 1/2 | 11 | B | 75.184 | 74.750 | 73.705 | 73.271 | 72.226
81.534 |  | G81.534x2.309 | G 2 3/4 | 11 | A | 81.534 | 81.100 | 80.055 | 79.838 | 78.576 |  |  | 78.576 | 79.216 | 80.055 | 80.272 | 81.534 |  | 69.8500 | 163.068 | 10.5000
81.534 |  | G81.534x2.309 | G 2 3/4 | 11 | B | 81.534 | 81.100 | 80.055 | 79.621 | 78.576
87.884 |  | G87.884x2.309 | G 3 | 11 | A | 87.884 | 87.450 | 86.405 | 86.188 | 84.926 |  |  | 84.926 | 85.566 | 86.405 | 86.622 | 87.884 |  | 76.2000 | 175.768 | 10.5000
87.884 |  | G87.884x2.309 | G 3 | 11 | B | 87.884 | 87.450 | 86.405 | 85.971 | 84.926
100.330 |  | G100.33x2.309 | G 3 1/2 | 11 | A | 100.330 | 99.896 | 98.851 | 98.634 | 97.372 |  |  | 97.372 | 98.012 | 98.851 | 99.068 | 100.330 |  | 88.9000 | 200.660 | 10.5000
100.330 |  | G100.33x2.309 | G 3 1/2 | 11 | B | 100.330 | 99.896 | 98.851 | 98.417 | 97.372
113.030 |  | G113.03x2.309 | G 4 | 11 | A | 113.030 | 112.596 | 111.551 | 111.334 | 110.072 |  |  | 110.072 | 110.712 | 111.551 | 111.768 | 113.030 |  | 101.6000 | 226.060 | 10.5000
113.030 |  | G113.03x2.309 | G 4 | 11 | B | 113.030 | 112.596 | 111.551 | 111.117 | 110.072
125.730 |  | G125.73x2.309 | G 4 1/2 | 11 | A | 125.730 | 125.296 | 124.251 | 124.034 | 122.772 |  |  | 122.772 | 123.412 | 124.251 | 124.468 | 125.730 |  | 114.3000 | 251.460 | 10.5000
125.730 |  | G125.73x2.309 | G 4 1/2 | 11 | B | 125.730 | 125.296 | 124.251 | 123.817 | 122.772
138.430 |  | G138.43x2.309 | G 5 | 11 | A | 138.430 | 137.996 | 136.951 | 136.734 | 135.472 |  |  | 135.472 | 136.112 | 136.951 | 137.168 | 138.430 |  | 127.0000 | 276.860 | 10.5000
138.430 |  | G138.43x2.309 | G 5 | 11 | B | 138.430 | 137.996 | 136.951 | 136.517 | 135.472
151.130 |  | G151.13x2.309 | G 5 1/2 | 11 | A | 151.130 | 150.696 | 149.651 | 149.434 | 148.172 |  |  | 148.172 | 148.812 | 149.651 | 149.868 | 151.130 |  | 139.7000 | 302.260 | 10.5000
151.130 |  | G151.13x2.309 | G 5 1/2 | 11 | B | 151.130 | 150.696 | 149.651 | 149.217 | 148.172
163.830 |  | G163.83x2.309 | G 6 | 11 | A | 163.830 | 163.396 | 162.351 | 162.134 | 160.872 |  |  | 160.872 | 161.512 | 162.351 | 162.568 | 163.830 |  | 152.4000 | 327.660 | 10.5000
163.830 |  | G163.83x2.309 | G 6 | 11 | B | 163.830 | 163.396 | 162.351 | 161.917 | 160.872

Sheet: BSP Pipe Threads
M Q | BSP-Rohrgewinde |  | Sort Order - 19 |  | External |  |  |  |  |  |  | Internal
 |  |  |  |  |  | Major Dia |  | Pitch Dia |  | Minor Dia |  |  | Minor Dia |  | Pitch Dia |  | Major Dia |  | Tap Drill | Thread Depth | Thread Runouts
Size | Size Suffix | Thread Designation | Custom Thread Designation | TPI | Class | Max | Min | Max | Min | Max | Min | Class | Min | Max | Min | Max | Min | Max | Basic |  | Basic
1/16 |  | G 1/16-28 | G 1/16-28 | 28 | A | 7.723 | 7.509 | 7.142 | 7.035 | 6.561 |  |  | 6.561 | 6.834 | 7.142 | 7.249 | 7.723 |  | 6.6000 | 15.4460 | 4.5000
1/16 |  | G 1/16-28 | G 1/16-28 | 28 | B | 7.723 | 7.509 | 7.142 | 7.035 | 6.561
1/8 |  | G 1/8-28 | G 1/8-28 | 28 | A | 9.728 | 9.514 | 9.147 | 9.040 | 8.566 |  |  | 8.566 | 8.848 | 9.147 | 9.254 | 9.728 |  | 8.7300 | 19.4560 | 4.5000
1/8 |  | G 1/8-28 | G 1/8-28 | 28 | B | 9.728 | 9.514 | 9.147 | 9.040 | 8.566
1/4 |  | G 1/4-19 | G 1/4-19 | 19 | A | 13.157 | 12.907 | 12.301 | 12.176 | 11.445 |  |  | 11.445 | 11.89 | 12.301 | 12.426 | 13.157 |  | 11.8000 | 26.3140 | 6.5000
1/4 |  | G 1/4-19 | G 1/4-19 | 19 | B | 13.157 | 12.907 | 12.301 | 12.176 | 11.445
3/8 |  | G 3/8-19 | G 3/8-19 | 19 | A | 16.662 | 16.412 | 15.806 | 15.681 | 14.950 |  |  | 14.95 | 15.395 | 15.806 | 15.931 | 16.662 |  | 15.2500 | 33.3240 | 6.5000
3/8 |  | G 3/8-19 | G 3/8-19 | 19 | B | 16.662 | 16.412 | 15.806 | 15.681 | 14.950
1/2 |  | G 1/2-14 | G 1/2-14 | 14 | A | 20.955 | 20.671 | 19.793 | 19.651 | 18.631 |  |  | 18.631 | 19.172 | 19.793 | 19.935 | 20.955 |  | 19.0500 | 41.9100 | 8.5000
1/2 |  | G 1/2-14 | G 1/2-14 | 14 | B | 20.955 | 20.671 | 19.793 | 19.651 | 18.631
5/8 |  | G 5/8-14 | G 5/8-14 | 14 | A | 22.911 | 22.627 | 21.749 | 21.607 | 20.587 |  |  | 20.587 | 21.128 | 21.749 | 21.891 | 22.911 |  | 21.0000 | 45.8220 | 8.5000
5/8 |  | G 5/8-14 | G 5/8-14 | 14 | B | 22.911 | 22.627 | 21.749 | 21.607 | 20.587
3/4 |  | G 3/4-14 | G 3/4-14 | 14 | A | 26.441 | 26.157 | 25.279 | 25.137 | 24.117 |  |  | 24.117 | 24.658 | 25.279 | 25.421 | 26.441 |  | 24.5000 | 52.8820 | 8.5000
3/4 |  | G 3/4-14 | G 3/4-14 | 14 | B | 26.441 | 26.157 | 25.279 | 25.137 | 24.117
7/8 |  | G 7/8-14 | G 7/8-14 | 14 | A | 30.201 | 29.917 | 29.039 | 28.897 | 27.877 |  |  | 27.877 | 28.418 | 29.039 | 29.181 | 30.201 |  | 28.2500 | 60.4020 | 8.5000
7/8 |  | G 7/8-14 | G 7/8-14 | 14 | B | 30.201 | 29.917 | 29.039 | 28.897 | 27.877
1 |  | G 1-11 | G 1-11 | 11 | A | 33.249 | 32.889 | 31.770 | 31.590 | 30.291 |  |  | 30.291 | 30.931 | 31.77 | 31.95 | 33.249 |  | 30.7500 | 66.4980 | 10.0000
1 |  | G 1-11 | G 1-11 | 11 | B | 33.249 | 32.889 | 31.770 | 31.590 | 30.291
1 1/4 |  | G 1 1/4-11 | G 1 1/4-11 | 11 | A | 41.910 | 41.550 | 40.431 | 40.251 | 38.952 |  |  | 38.952 | 39.592 | 40.431 | 40.611 | 41.910 |  | 39.5000 | 83.8200 | 10.0000
1 1/4 |  | G 1 1/4-11 | G 1 1/4-11 | 11 | B | 41.910 | 41.550 | 40.431 | 40.251 | 38.952
1 1/2 |  | G 1 1/2-11 | G 1 1/2-11 | 11 | A | 47.803 | 47.443 | 46.324 | 46.144 | 44.845 |  |  | 44.845 | 45.485 | 46.324 | 46.504 | 47.803 |  | 45.5000 | 95.6060 | 10.0000
1 1/2 |  | G 1 1/2-11 | G 1 1/2-11 | 11 | B | 47.803 | 47.443 | 46.324 | 46.144 | 44.845
1 3/4 |  | G 1 3/4-11 | G 1 3/4-11 | 11 | A | 53.746 | 53.386 | 52.267 | 52.087 | 50.788 |  |  | 50.788 | 51.428 | 52.267 | 52.447 | 53.746 |  | 51.0000 | 107.4920 | 10.0000
1 3/4 |  | G 1 3/4-11 | G 1 3/4-11 | 11 | B | 53.746 | 53.386 | 52.267 | 52.087 | 50.788
2 |  | G 2-11 | G 2-11 | 11 | A | 59.614 | 59.254 | 58.135 | 57.955 | 56.656 |  |  | 56.656 | 57.296 | 58.135 | 58.315 | 59.614 |  | 57.0000 | 119.2280 | 10.0000
2 |  | G 2-11 | G 2-11 | 11 | B | 59.614 | 59.254 | 58.135 | 57.955 | 56.656
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

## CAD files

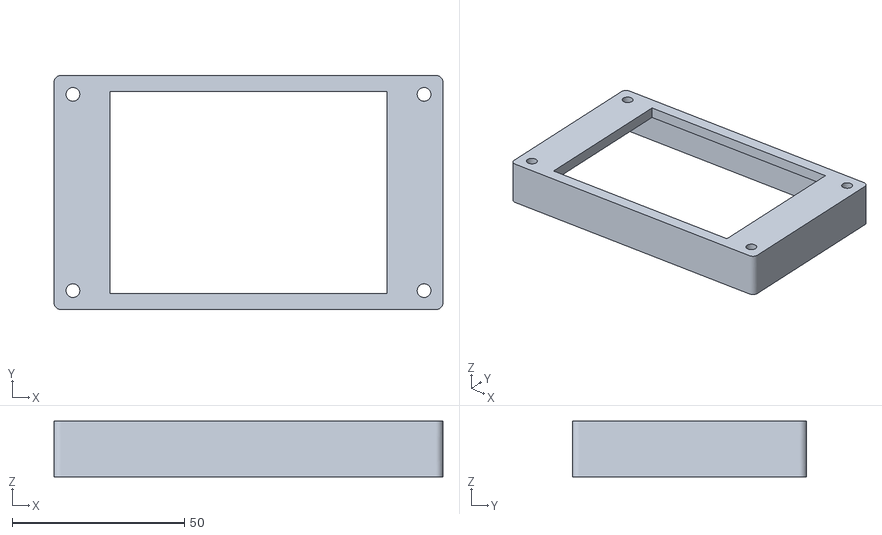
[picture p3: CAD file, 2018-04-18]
stl/mks_tft32_case_front.stl
113.0 x 68.0 x 16.2

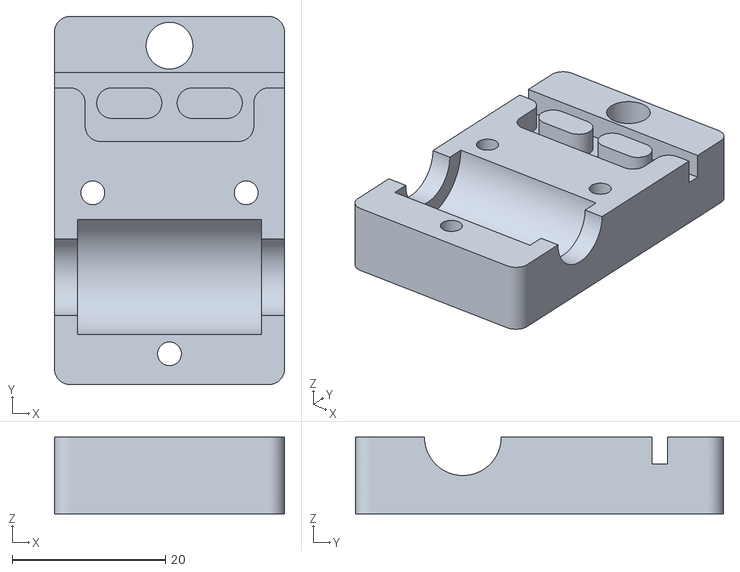
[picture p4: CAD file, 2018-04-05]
stl/xy_bearing_block.stl
30.0 x 48.0 x 10.0

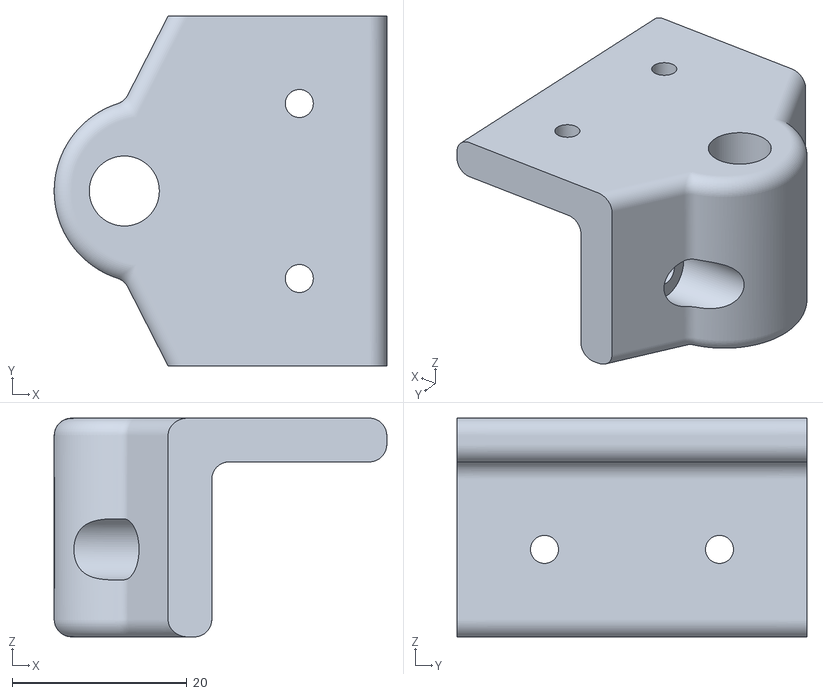
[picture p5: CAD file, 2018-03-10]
stl/Spoolholder - Extrusion Mount.stl
38.0 x 40.0 x 25.0

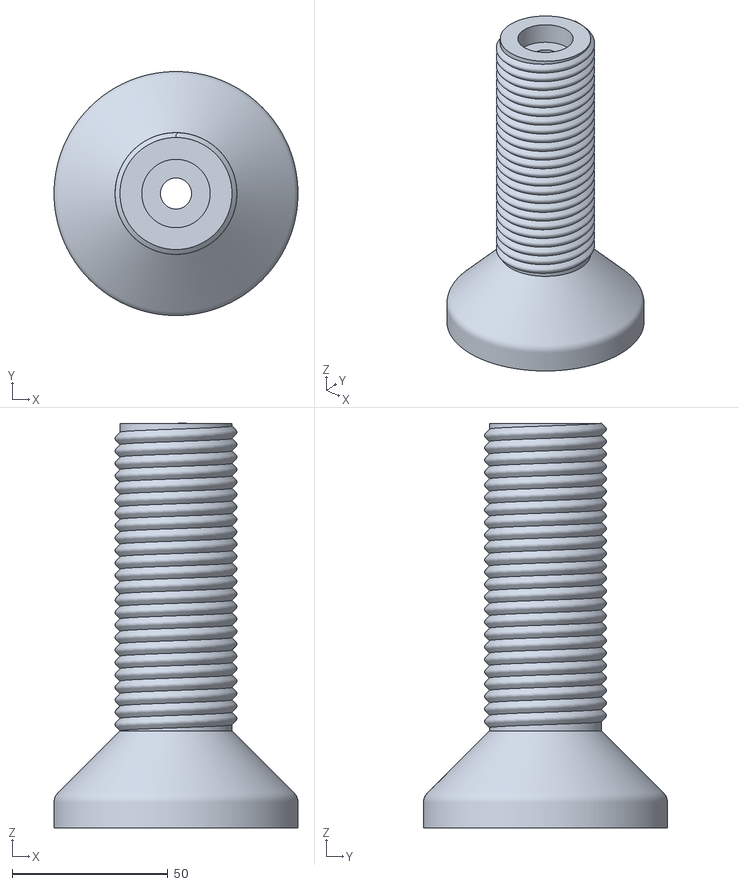
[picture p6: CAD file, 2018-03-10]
stl/Spoolholder - Axle .stl
78.4 x 78.4 x 130.2

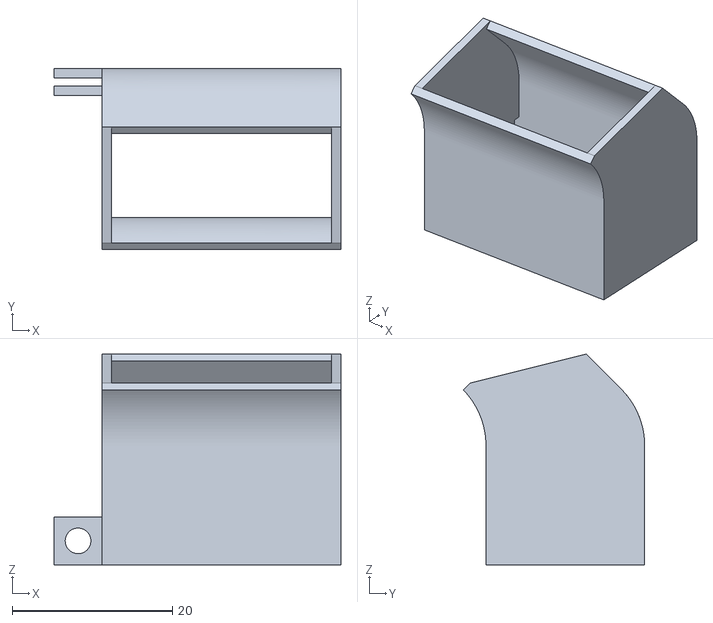
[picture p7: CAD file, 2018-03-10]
stl/fan_duct_volcano_1.stl
35.8 x 22.6 x 26.3

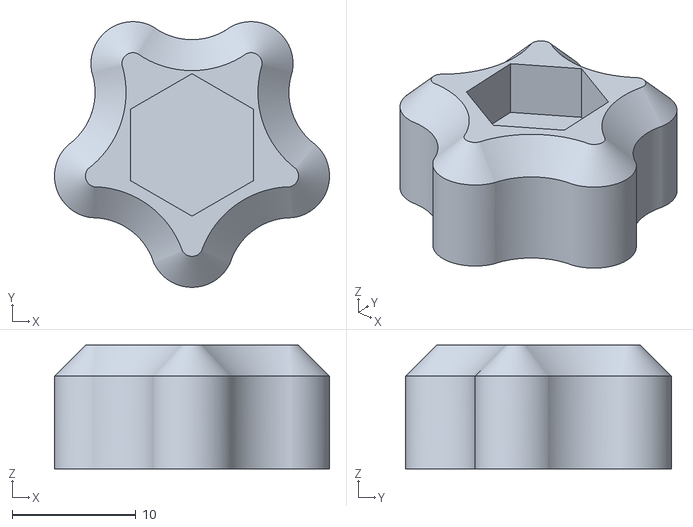
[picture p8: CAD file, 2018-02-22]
stl/rubber_damper.stl
22.2 x 21.5 x 10.0

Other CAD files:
cad/Templates/Englisch/am_ansi.dwg
cad/Templates/Metrisch/am_iso.dwg
cad/Templates/Norm.dwg
documentation/middle plate.dwg
cad/Templates/Englisch/ANSI (Zoll).dwg
cad/Templates/Metrisch/GOST.dwg
cad/Templates/Metrisch/GB.dwg
cad/Templates/Metrisch/JIS.dwg
cad/Templates/Metrisch/am_bsi.dwg
cad/Templates/Metrisch/DIN.dwg
cad/Templates/Metrisch/ISO.dwg
cad/Templates/Metrisch/am_gb.dwg
cad/1166-B2P-A.ipt
cad/1167-B2P-A (2).ipt
cad/290mm.ipt
cad/30mm Fan.ipt
cad/330mm.ipt
cad/375 - 8 (4 start) acme thread.ipt
cad/400mm.ipt
cad/40mm fan.ipt
cad/500mm.ipt
cad/5mm to 8mm flexible shaft coupler x.ipt
cad/8mm hardened rod.ipt
cad/Alu Ramen.iam
cad/Clamp.ipt
cad/CoreBot.iam
cad/Corner Piece.ipt
cad/Design Data/AIT/Mold Design/mold design stop pin.ipt
cad/Design Data/Cable & Harness/de-DE/harness.iam
cad/Design Data/Tube & Pipe/de-DE/piping runs.iam
cad/DriveLine 8x350mm.ipt
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

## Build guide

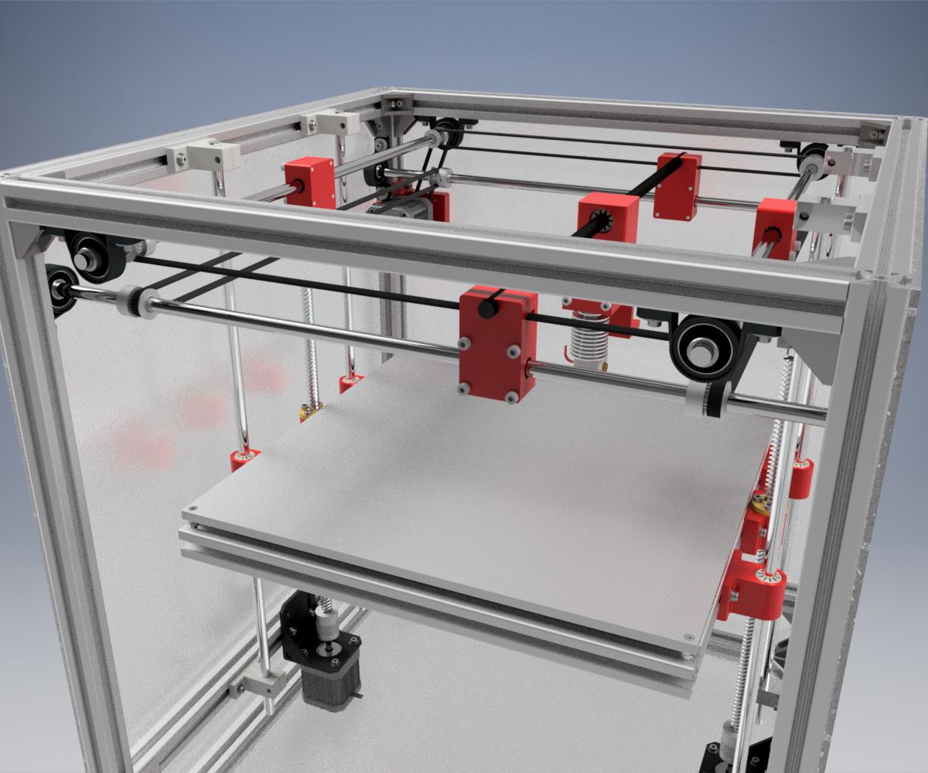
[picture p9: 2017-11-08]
media/prebuild render 06.jpg

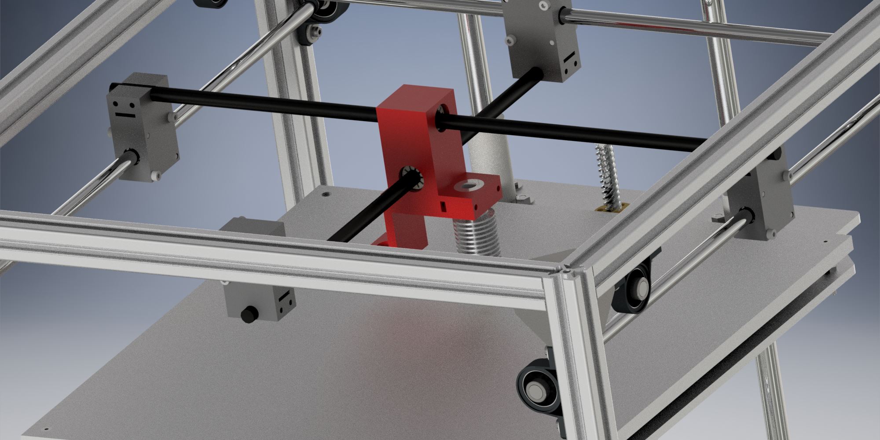
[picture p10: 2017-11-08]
media/prebuild render 02.jpg

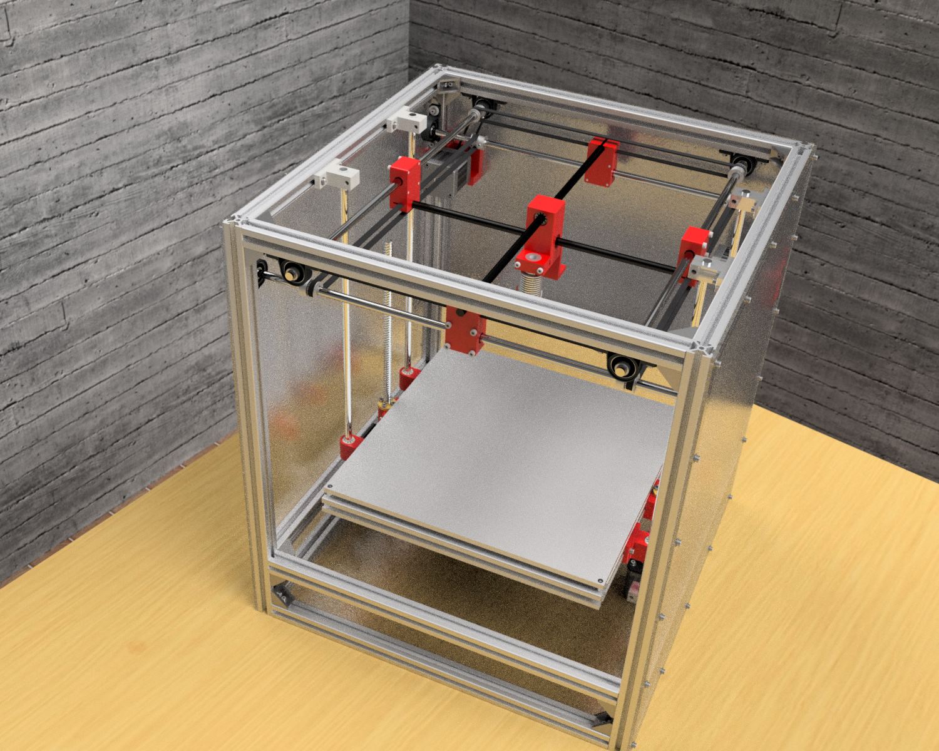
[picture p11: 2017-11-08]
media/prebuild render 11.jpg

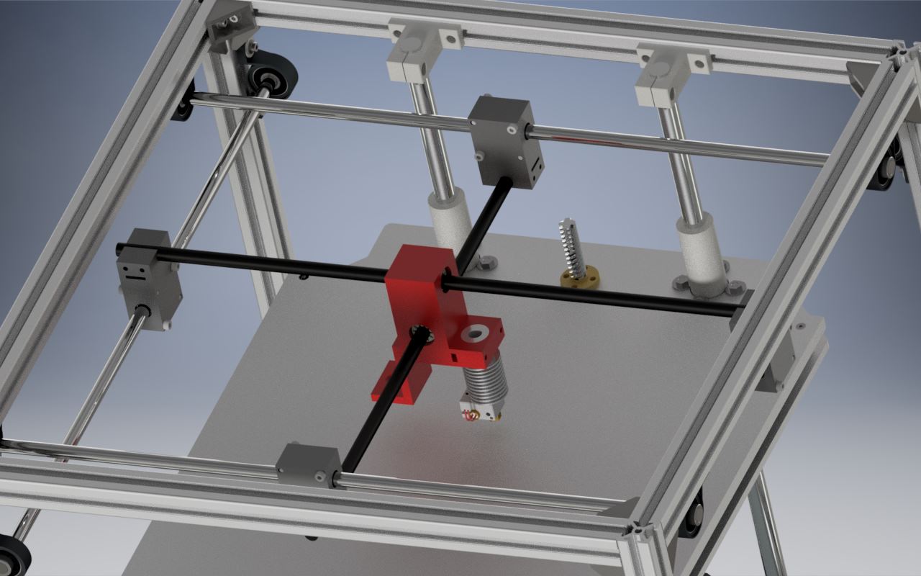
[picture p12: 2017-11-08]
media/prebuild render 01.jpg

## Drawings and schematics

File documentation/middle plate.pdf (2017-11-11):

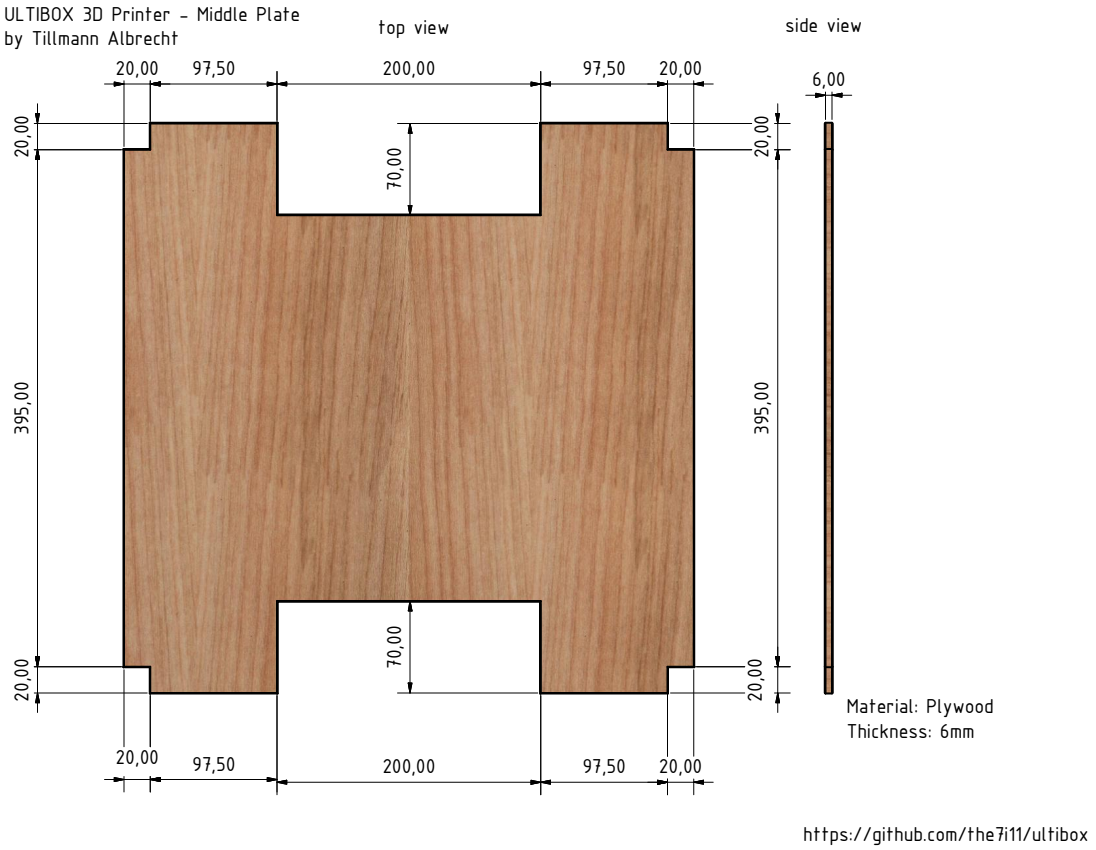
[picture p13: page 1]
top view; side view; Material: Plywood Thickness: 6mm

ULTIBOX 3D Printer - Middle Plate
by Tillmann Albrecht

https://github.com/the7i11/ultibox

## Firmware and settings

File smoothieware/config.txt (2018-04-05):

# NOTE Lines must not exceed 132 characters
# Robot module configurations : general handling of movement G-codes and slicing into moves
default_feed_rate                            10000            # Default rate ( mm/minute ) for G1/G2/G3 moves
default_seek_rate                            3000             # Default rate ( mm/minute ) for G0 moves
mm_per_arc_segment                           0.2              # Arcs are cut into segments ( lines ), this is the length for
                                                              # these segments.  Smaller values mean more resolution,
                                                              # higher values mean faster computation
mm_per_line_segment                          5                # Lines can be cut into segments ( not usefull with cartesian
                                                              # coordinates robots ).

# Arm solution configuration : Cartesian robot. Translates mm positions into stepper positions
alpha_steps_per_mm                           320               # Steps per mm for alpha stepper
beta_steps_per_mm                            320               # Steps per mm for beta stepper
gamma_steps_per_mm                           800              # Steps per mm for gamma stepper

# Planner module configuration : Look-ahead and acceleration configuration
planner_queue_size                           32               # DO NOT CHANGE THIS UNLESS YOU KNOW EXACTLY WHAT YOU ARE DOING
acceleration                                 2000              # Acceleration in mm/second/second.
z_acceleration                               60               # Acceleration for Z only moves in mm/s^2, 0 uses acceleration which is the default. DO NOT SET ON A DELTA
acceleration_ticks_per_second                1000             # Number of times per second the speed is updated
junction_deviation                           0.02             # Similar to the old "max_jerk", in millimeters,
                                                              # see https://github.com/grbl/grbl/blob/master/planner.c
                                                              # and https://github.com/grbl/grbl/wiki/Configuring-Grbl-v0.8
                                                              # Lower values mean being more careful, higher values means being
                                                              # faster and have more jerk
#z_junction_deviation                        0.0              # for Z only moves, -1 uses junction_deviation, zero disables junction_deviation on z moves DO NOT SET ON A DELTA
#minimum_planner_speed                       0.0              # sets the minimum planner speed in mm/sec





# Stepper module configuration
microseconds_per_step_pulse                  1                # Duration of step pulses to stepper drivers, in microseconds
base_stepping_frequency                      100000           # Base frequency for stepping, higher gives smoother movement

# Cartesian axis speed limits
x_axis_max_speed                             400*60            # mm/min
y_axis_max_speed                             400*60            # mm/min
z_axis_max_speed                             40*60              # mm/min

# Stepper module pins ( ports, and pin numbers, appending "!" to the number will invert a pin )
alpha_step_pin                               2.0              # Pin for alpha stepper step signal
alpha_dir_pin                                0.5!             # Pin for alpha stepper direction
alpha_en_pin                                 0.4              # Pin for alpha enable pin
alpha_current                                2              # X stepper motor current
alpha_max_rate                               12000.0          # mm/min

beta_step_pin                                2.1              # Pin for beta stepper step signal
beta_dir_pin                                 0.11!             # Pin for beta stepper direction
beta_en_pin                                  0.10             # Pin for beta enable
beta_current                                 2              # Y stepper motor current
beta_max_rate                                12000.0          # mm/min

gamma_step_pin                               2.2              # Pin for gamma stepper step signal
gamma_dir_pin                                0.20            # Pin for gamma stepper direction
gamma_en_pin                                 0.19             # Pin for gamma enable
gamma_current                                1.5              # Z stepper motor current
gamma_max_rate                               40*60.0            # mm/min

epsilon_current      			     1.5

# Serial communications configuration ( baud rate default to 9600 if undefined )
uart0.baud_rate                              115200           # Baud rate for the default hardware serial port
second_usb_serial_enable                     true             # This enables a second usb serial port (to have both pronterface
                                                              # and a terminal connected)
pause_button_enable                          true             # Pause button enable


# Extruder module configuration
extruder.hotend.enable                          true             # Whether to activate the extruder module at all. All configuration is ignored if false
extruder.hotend.steps_per_mm                    837               # Steps per mm for extruder stepper
extruder.hotend.default_feed_rate               600              # Default rate ( mm/minute ) for moves where only the extruder moves
extruder.hotend.acceleration                    500              # Acceleration for the stepper motor, as of 0.6, arbitrary ratio
extruder.hotend.max_speed                       60               # mm/s

extruder.hotend.step_pin                        2.3              # Pin for extruder step signal
extruder.hotend.dir_pin                         0.22!            # Pin for extruder dir signal
extruder.hotend.en_pin                          0.21             # Pin for extruder enable signal

delta_current                                2              # First extruder stepper motor current


# Hotend temperature control configuration
temperature_control.hotend.enable            true             # Whether to activate this ( "hotend" ) module at all.
                                                              # All configuration is ignored if false.
temperature_control.hotend.thermistor_pin    0.24             # Pin for the thermistor to read
temperature_control.hotend.heater_pin        2.7              # Pin that controls the heater, set to nc if a readonly thermistor is being defined   2.7
temperature_control.hotend.beta             3950              # or set the beta value
temperature_control.hotend.set_m_code        104              #
temperature_control.hotend.set_and_wait_m_code 109            #
temperature_control.hotend.designator        T                #

#temperature_control.hotend.p_factor         13.7             # permanently set the PID values after an auto pid
#temperature_control.hotend.i_factor         0.097            #
#temperature_control.hotend.d_factor         24               #

#temperature_control.hotend.max_pwm          255               # max pwm, 64 is a good value if driving a 12v resistor with 24v.


temperature_control.bed.enable               true             #
temperature_control.bed.thermistor_pin       0.23             #
temperature_control.bed.heater_pin           2.5              #  2.5
temperature_control.bed.beta                 3960             # or set the beta value
temperature_control.bed.pwm_frequency	     5
temperature_control.bed.bang_bang	     true	     
temperature_control.bed.set_m_code           140              #
temperature_control.bed.set_and_wait_m_code  190              #
temperature_control.bed.designator           B                #


# Switch module for fan control
switch.fan.enable                            true             #
switch.fan.input_on_command                  M106             #
switch.fan.input_off_command                 M107             #
switch.fan.output_pin                        2.4              #
switch.fan.output_type                       pwm              # pwm output settable with S parameter in the input_on_comand
switch.fan.max_pwm                           64               # set max pwm for the pin default is 255

switch.hotendfan.enable                           true             #
switch.hotendfan.input_on_command                 M42              #
switch.hotendfan.input_off_command                M43              #
switch.hotendfan.output_pin                       2.6              #
switch.hotendfan.output_type                      pwm              # 
switch.hotendfan.max_pwm                           110
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

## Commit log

2017-11-08 First commit of everything I have - hope it's enought!
    [1166-B2P-A.ipt, 1167-B2P-A (2).ipt, 290mm.ipt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]
2017-11-08 Added bill of material
    [BOM.xlsx]
2017-11-11 cleaned up CAD structure
    [Ultibox.0070.iam, Ultibox.iam, Z gantry.0043.iam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]
2017-11-11 added middle plate and drawing a of it
    [Alu Ramen.0033.iam, Alu Ramen.iam, middle plate.0001.dwg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]
2017-11-13 changed hotend mount to accept various air ducts
    [Hotend Mount 2.2.ipt]
2017-11-13 some cosmetic changes
    [Alu Ramen.0033.iam, Alu Ramen.iam, BOM.xlsx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]
2017-11-16 added first simple modular fanduct
    [fan duct 1.ipt, fan_duct_1.stl]
2017-11-16 further progress with the case for the RepRap Discount LCD
    [case rear.ipt, controller case.iam, smart_controller_case_front.stl]
2017-11-16 added rear part of the lcd case
    [case front.ipt, case rear.ipt, controller case.iam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]
2017-11-18 changed the z-axis bearings against proper LM8LUU type
    [UM gantry.iam, Ultibox.iam, Z flange.iam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]
2017-11-18 added some rubber-damped feet to the frame
    [Alu Ramen.iam, M6x20.ipt, Ultibox.iam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]
2018-02-22 Added Cura printing profile
    [Ultibox+1.0.global.cfg]
2018-02-22 STL file for rubber feet available
    [rubber_damper.stl]
2018-02-22 changed nomenclature
    [Hotend 2.2.iam, UM gantry.iam, Ultibox.iam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]
2018-03-01 added inductive probe
    [M8 inductive probe.ipt]
2018-03-01 added smoothieware files
    [config.txt]
2018-03-01 build some E3D-Hardware on my own
    [E3D-v6 1.75mm Heat Break.ipt, E3D-v6 Volcano Heater Block.ipt, E3D-v6 Volcano Nozzle.0002.ipt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]
2018-03-01 made mounting holes for part cooling fan deeper
    [Hotend 2.2.iam, Hotend Mount 2.2.ipt, UM gantry.iam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]
2018-03-10 Added cooling air duct for E3D Volcano
    [40mm fan.ipt, fan_duct_volcano_1.stl, shroud 01 volcano.ipt]
2018-03-10 Added a filament spool holder that fits even 2,5kg spools
    [Spoolholder - Axle .stl, Spoolholder - Extrusion Mount.stl, Spoolholder - Nut.stl]
2018-03-10 updated cooling fan model, but only for a optically more pleasing one
    [Hotend 2.2.iam, UM gantry.iam, Ultibox.iam]
2018-03-11 Added two rendered images of the hotend and the whole printer
    [Hotend 2.2.iam, Hotend Mount 2.2.ipt]
2018-04-05 started design of MKS TFT32 case
    [MKS TFT.iam, MKS TFT32.ipt, front_case.ipt]
2018-04-05 Embedded the screw heads and nuts into the xy sliding blocks
    [Lagerblock XY.ipt, UM gantry.iam, Ultibox.iam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]
2018-04-18 Added STL for mks TFT32
    [mks_tft32_case_front.stl]
